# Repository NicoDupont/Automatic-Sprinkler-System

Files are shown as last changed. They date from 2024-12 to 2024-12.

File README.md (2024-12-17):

# Arrosage Automatique

A diy project to automate my irrigation system.  

Last Update : 17/12/2024  
This is the second working version for summer 2024, it will be adapted for 2025 if needeed and time available.

- python scripts improved
- webapp improved
- mqtt improved
- overall improvement of functionality

**Minimum Requirements :**

- A Raspberry pi 2 >= with python 3.8.x

- A webserver for the web app

- A database like mariadb/mysql (not tested with another db)

**Main Goal : replace one or more irrigation controllers and do it by mylself.**    

 **Big Concept :**

- Logic is done by python scripts on a raspberry pi

- Data management is done with an sql data base, mqtt is used to monitor and control the systeme from HA

- UI is based on a web application (home assistant can be used too(with mqtt))

- Sensors data comes from home-assistant/esphome
  
  **Overall functional descriptions :**

- A WebApp allows me to manage each solenoid valve/zone, global parameters, see the latest events, the watering sequence and some data.

- A collection of python scripts are used to open or close the solenoid valves and compute the watering sequence(s). 
  
  - There is a winter/stop, test, sequence on demande, automatic and manual mode
  - The program checks some data to know if it can run watering
  - Status and events are recorded in the database, sent to an mqtt broker and displayed on an LCD screen
  - Several zones and/or sequences can run simultaneously (depends on the power supply for the solenoid valve and the watering pump)

- config.py file is used to configure the script in addition with the database.

- I can bypass the programmation to directly power supply and open any solenoid valve I want with 3 positions switch wired for each solenoid valve.

- Mqtt autodiscovery for homeassistant can be used (first test for diagnostics and not finish actualy)

- There are a few built-in automations : max number of active solenoid valve active at the same time, rainfall, test if one sequence is between 2 days,  calculate the coef duration in correlation with the outside temperature...

**Side projects (in progress) :**

- Tank filling  [link](https://github.com/NicoDupont/esp_remplissage_cuve)
- [in progress] PCB for relays, lcd, rtc module [link](https://github.com/NicoDupont/PCB/tree/main/arrosage)
- Irrigation circuit monitoring  [link](https://github.com/NicoDupont/Monitoring_Arrosage)
- [in progress] Tank monitoring  [link](https://github.com/NicoDupont/Monitoring_Cuve_Arrosage)

**Futur improvements :**

- Mqtt : redo/complete mqtt parts with complete autodiscovery in HA (no need to add entities in configuration.yaml and add cmd/state topic)
- The WebApp will be split into two components: Front + Api Back
- Possibility to put a zone in more than 1 sequence
- Clean and redo the watering box (electricity+electronics)

**Current limitations :**

- A sequence/zone cannot be straddled between 2 days due to the very simple operation of the programming
- All parameters cannot be updated from home assistant
- Events are visible only from the web interface
- web app is not complete

**Folder organisation :**

    | IrriPi
      => | App ( simple web app )
         | Docs  
         | rpi (python logic)
         readme.md

**Raspberry Pi requirements :** 

<b>Config.txt :</b>  
In the event of an unexpected restart, this will allow not to open a solenoid valve by mistake.  
I need to add the following to the config.txt file to force gpio output and high state on gpio during the boot sequence :    

> gpio=4-13=op,dh  
> gpio=16-27=op,dh 

Gpio 2,3 are used for I2C (rtc and lcd)  
Gpio 14-15 are reserved and cannot be used !   

=> 22 gpio are therefore usable  

#### Start Watering at start

<b>Cron :</b>  
in contrab -e:

> @reboot sleep 20; sh /home/pi/launcher_arrosage.sh

<b>best solution by creating services with systemd</b>

For each Python file (main.py, automation.py, mqtt_publish.py mqtt_subscribe.py)

- arrosage-main
- arrosage-automation
- arrosage-publisher
- arrosage-subscriber

```bash
sudo nano /etc/systemd/system/arrosage-main.service

[Unit]
Description=Arrosage Main
After=network-online.target sysinit.target
Wants=network-online.target sysinit.target

[Service]
User=pi
WorkingDirectory=/home/pi/arrosage
ExecStart=/usr/bin/python3 /home/pi/arrosage/main.py
Restart=always
RestartSec=5

[Install]
WantedBy=multi-user.target

#update systemed
sudo systemctl daemon-reload
#enable service
sudo systemctl enable arrosage-main.service
#status
sudo systemctl status arrosage-main.service
#start
sudo systemctl start arrosage-main.service
#stop
sudo systemctl stop arrosage-main.service
#restart
sudo systemctl restart arrosage-main.service
```

<b>Raspi-config :</b>  

- i2c must be activated (rtc + lcd)
- spi must be deactivated  

<b>Mqtt autodiscovery in home assistant :</b>    

> run : python3 /home/pi/arrosage/mqtt_autodiscovery.py     

**Functional Diagram :**

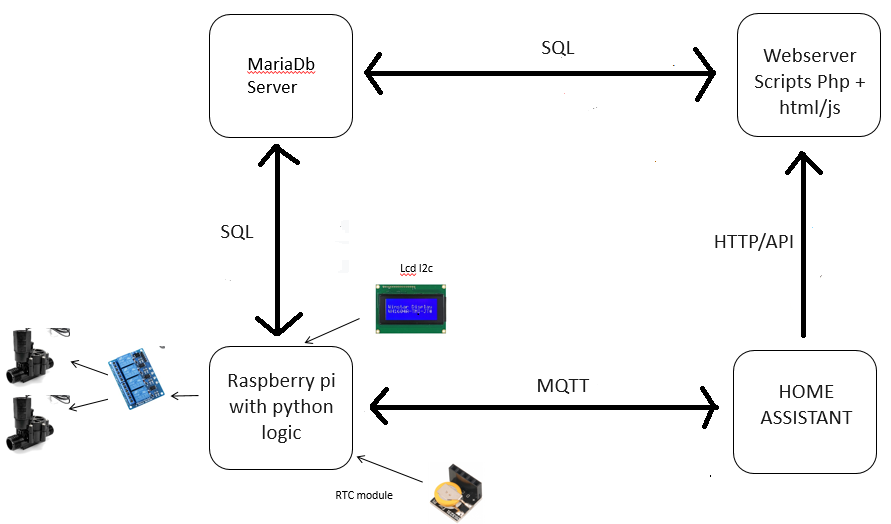
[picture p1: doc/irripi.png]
Functional_Diagram


**Watering parts**

- I use rainbird dv100 24vac solenoid valve

**Electric Parts**

- 1x Circuit breaker 2A 230v
- 1x Electrical outlet 230v
- 1x AC 24v 1,6A output rail din power supply (for solenoid valves) [links](https://www.amazon.fr/gp/product/B00F4QIL06/ref=ppx_yo_dt_b_asin_title_o02_s00?ie=UTF8&psc=1)
- 1x DC 5v 2.5A output power supply (for raspberry, esp8266, relay, electronic...)

Electronics_Box

**Electronics Parts**

- Raspberry Pi 2b + micro sd 
- 22x relay 5v
- 22x button 3 positions
- 1x button 2 positions
- 23x Screw Fuse Terminal Block rail din [links](https://fr.aliexpress.com/item/32957557760.html?spm=a2g0o.order_list.0.0.21ef5e5bLPmCsD&gatewayAdapt=glo2fra)
- 22x fuse 20x5 0.5A
- 1x fuse 20x5 2A
- 1x lcd 20x4 i2c 5v
- 1x rtc module DS3231 i2c 3.3v

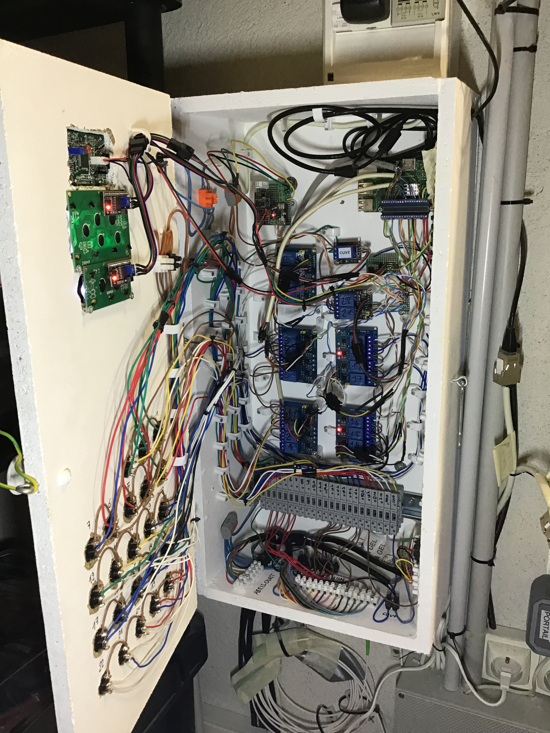
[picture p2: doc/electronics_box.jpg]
Electronics_Box

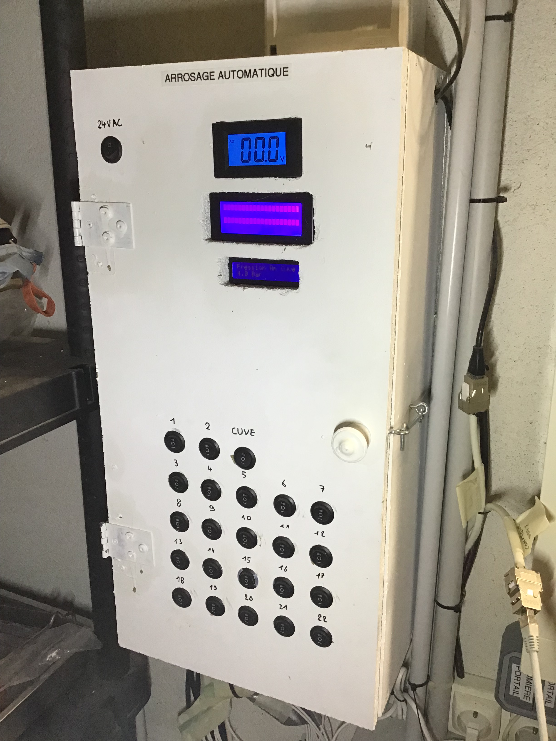
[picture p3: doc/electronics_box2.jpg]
Electronics_Box


**Web App :**

The web app  :  

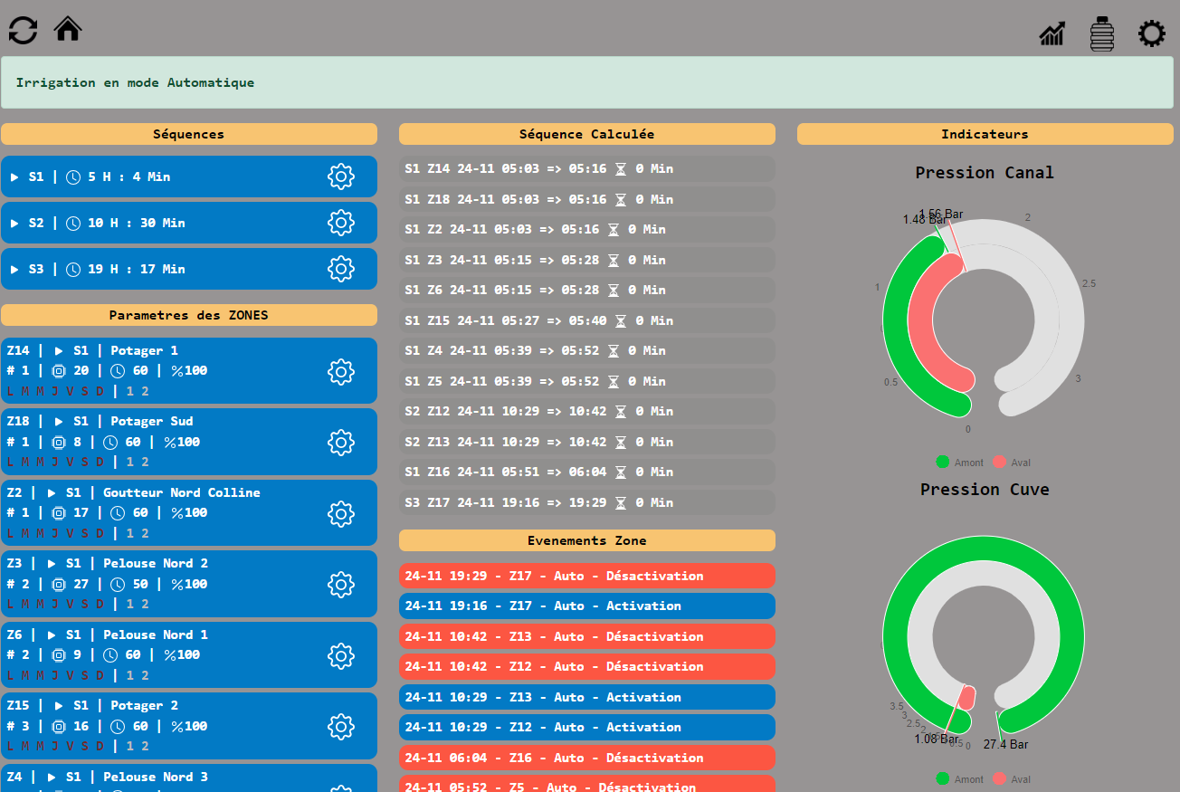
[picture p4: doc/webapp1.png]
web app irripi


**Schematic :**

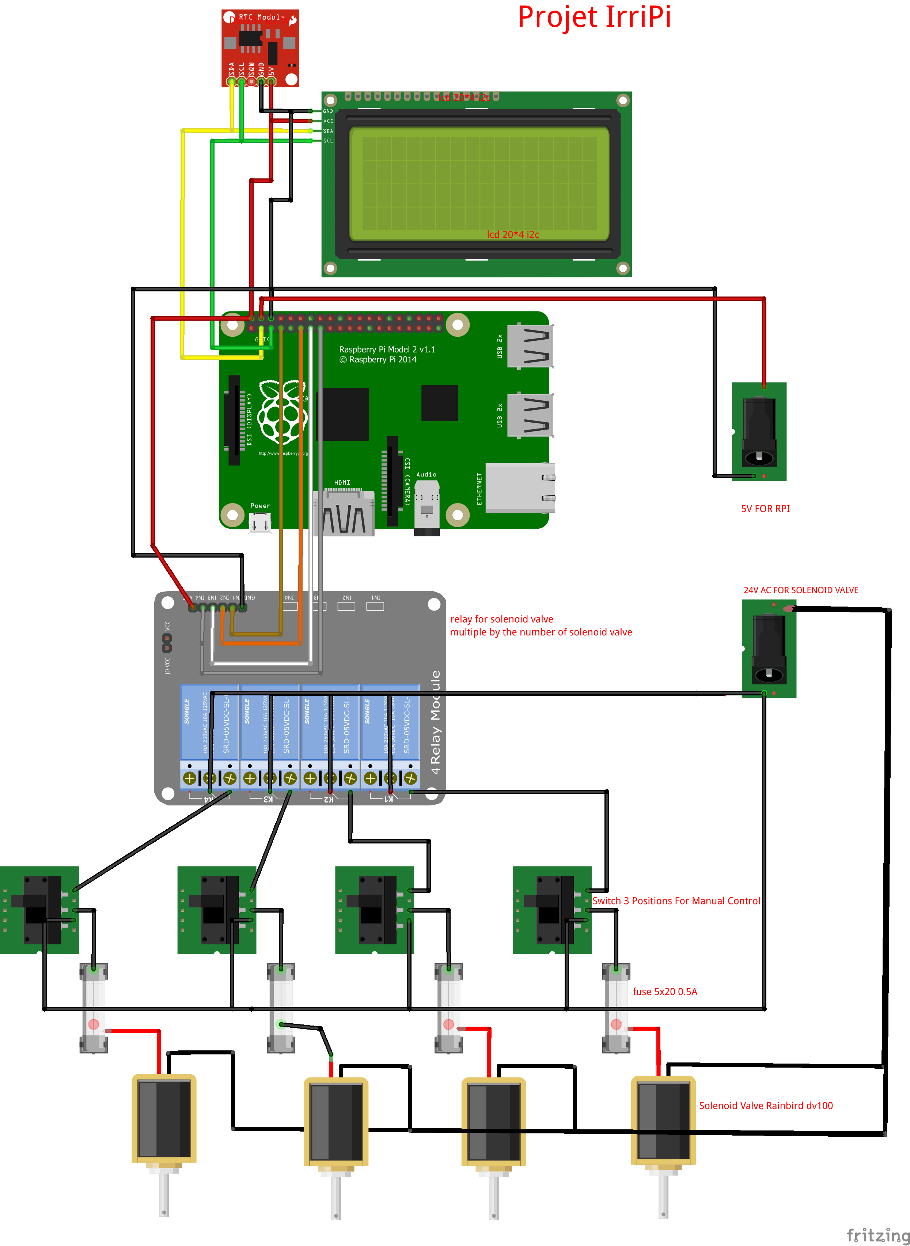
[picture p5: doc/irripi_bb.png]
fritzing irripi rpi


**Integration in [Home-Assistant](https://www.home-assistant.io/)**

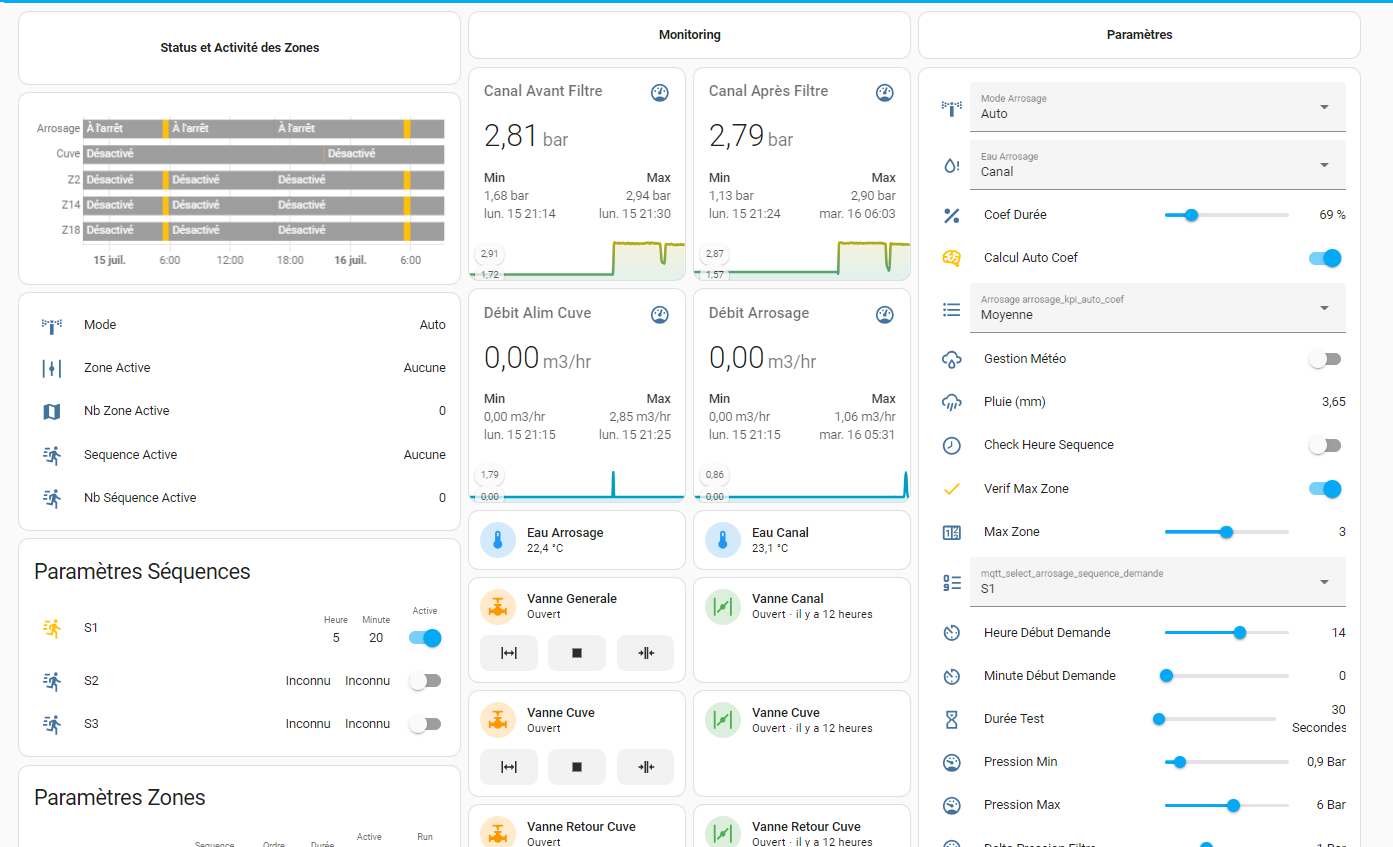
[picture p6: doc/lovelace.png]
Home-Assistant lovelace

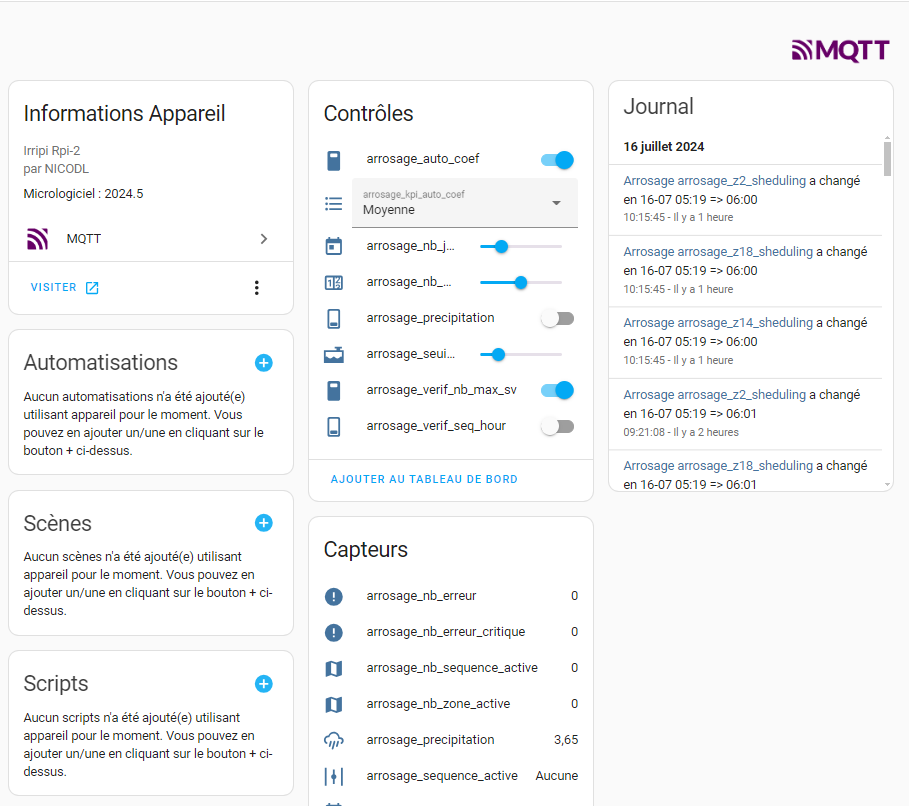
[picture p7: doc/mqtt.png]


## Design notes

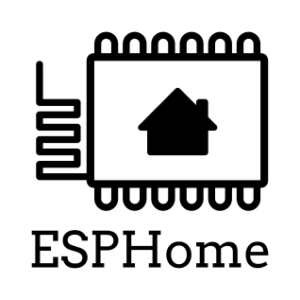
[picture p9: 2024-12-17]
webapp/img/esphome.png

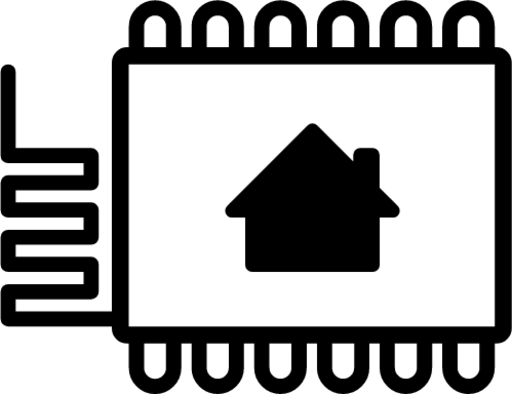
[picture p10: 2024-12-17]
webapp/img/esphome2.png

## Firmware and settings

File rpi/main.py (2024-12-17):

"""
* -----------------------------------------------------------------------------------
* Last update :   24/10/2024
* Arrosage Automatique / IrriPi
* Main launch script
* -----------------------------------------------------------------------------------
"""
#conda install -c conda-forge mysql-connector-python
# if numpy error on raspberrypi :
#sudo apt-get install python-dev libatlas-base-dev 
from watering import Watering
from sequence import ComputeSequence
from anomaly import AnomalyDetection,MqttStatusAnomaly
import function as func
import yaml
import time
import RPi.GPIO as GPIO
#import pandas as pd
import logging
import datetime
import pandas as pd

if __name__ == '__main__':
    #---------------------------------------
    # parameters for the script from config.yaml 
    import config as config

    GPIO.setwarnings(False)
    GPIO.cleanup()
    GPIO.setmode(GPIO.BCM)
    for gpio in config.list_gpio:
        GPIO.setup(gpio, GPIO.OUT)
        GPIO.output(gpio, GPIO.HIGH)

    #--------------------------------------
    #initialise logging config
    #jour = GetDayTime(0)
    logger = logging.getLogger(__name__)#.addHandler(logging.NullHandler())
    #logfile = "log/arrosage_"+str(jour.day)+"_"+str(jour.month)+"_" +str(jour.year)+".txt"
    logfile = "log/arrosage.txt"
    func.ConfigLogging(logger,logfile,config.LOG_LEVEL_STREAM,config.LOG_LEVEL_FILE,True)

    #https://stackoverflow.com/questions/5974273/python-avoid-passing-logger-reference-between-functions
    #---------------------------------------
    # NUMBER_LOOP
    i=0
    cpt_error = 0
    cpt_info = 0
    
    while True: #loop launch
        i+=1
        cpt_info+=1
        try:
            engine,connection = func.DbConnect(logger)
            func.AddMqttQueue(i,"status/loop_main",connection,logger)#to know if running
            func.AddMqttQueue(cpt_error,'status/loop_main_erreur',connection,logger)#to know if error
            try:
                actual_day = func.GetDayTime(0)
                #prev_day = GetDayTime(-1) 
                # ----------------------------------------------------
                # global settings 
                global_settings = func.LoadData('select * from Parameter limit 1',logger,connection,file=config.GLOBAL_SETTINGS_FILE)
                global_coef = global_settings["coef"].iloc[0]
                mode = global_settings["mode"].iloc[0]
                sequence_demande = global_settings["sequence_demande"].iloc[0]
                heure_demande = global_settings["heure_demande"].iloc[0]
                minute_demande = global_settings["minute_demande"].iloc[0]
                logger.debug(f'mode arrosage: {mode}')
                # ----------------------------------------------------
                # sequences settings
                sequence_settings = func.LoadData('select * from Sequence where active=1',logger,connection,file=config.SEQUENCE_FILE)
                # ----------------------------------------------------
                # zones settings
                zone_settings = func.LoadData("""select a.id_sv,a.type,a.sv,a.order,a.gpio,a.name,a.open,
                                              (case when b.active=0 then 0 else a.active end) as active,
                                              a.sequence,a.duration,a.test,a.even,a.odd,a.monday,a.tuesday,
                                              a.wednesday,a.thursday,a.friday,
                                              a.saturday,a.sunday,a.coef,a.rpi 
                                              from Zone as a 
                                              left join Sequence as b on a.sequence=b.seq 
                                              where a.type='zone'""",logger,connection,file=config.ZONE_PARAMETER_FILE)
                logger.debug("Zone:")
                logger.debug(zone_settings.head())
                # ----------------------------------------------------
                # calculate the solenoid valve launch sequence by sequence and order
                zone_active = zone_settings[zone_settings.active.eq(1)]
                logger.debug("Zone active:")
                logger.debug(zone_active.head())
                # ----------------------------------------------------
                # iterate over sequence to compute each sequence 

                ##################################################################################################
                # modifier cette partie car conflit quand plusieurs sequences actives et revoir le mode à la demande
                if not sequence_settings.empty and not zone_active.empty:
                    zone_sequence = pd.DataFrame()
                    for index, row in sequence_settings.iterrows():
                        sequence = row["seq"]
                        hstart = row["heure"]
                        mstart = row["minute"]
                        
                        if mode == 'Demande' and sequence_demande==sequence:
                            starting_date = datetime.datetime(actual_day.year, actual_day.month, actual_day.day,hour=int(heure_demande),minute=int(minute_demande))
                        else:
                            starting_date = datetime.datetime(actual_day.year, actual_day.month, actual_day.day,hour=int(hstart),minute=int(mstart))

                        params_compute_sequence = {
                            'sequence_number':sequence,
                            'reference_date':starting_date,
                            'zone':zone_active[zone_active.sequence.eq(sequence)],
                            'global_time_coefficient':global_coef,
                            'delay_time_sequence':config.DELAY_TIME_SEQUENCE,
                            'min_runtime':config.MIN_TIME_SEQUENCE,
                            'max_runtime':config.MAX_TIME_SEQUENCE,
                            'logger':logger
                        }
                        #calculation of the sequence for the watering zones by sequence number
                        zs = pd.DataFrame()
                        zs = ComputeSequence(**params_compute_sequence)
                        logger.debug("Zone Sequence:")
                        logger.debug(f"zone :{sequence}")
                        logger.debug(zone_sequence.head())
                        if not zs.empty:
                            if zone_sequence.empty:
                                zone_sequence = zs
                            else:
                                zone_sequence = pd.concat([zone_sequence,zs], ignore_index=True)
                            
                    zone_active = zone_active.merge(zone_sequence, how='left', on=['order','sequence'])
                    #filter data if no sequence active and add boolean if sv is planned today.
                    #logger.info(zone_active.head(15))
                    zone_active['planned']=zone_active.apply(lambda row: func.IsProgrammed(row["sv"],row["StartingDate"],row["EndDate"],actual_day,row["even"],row["odd"],row["monday"],row["tuesday"],row["wednesday"],row["thursday"],row["friday"],row["saturday"],row["sunday"],True,logger), axis=1)
                    zone_active= zone_active[zone_active['StartingDate'].notnull()]
                    # update calculated sequences to the database
                    #logger.info(zone_active.head())
                    func.UpdateSequence('SequenceZone',zone_active[['id_sv','sv','name','sequence','order','open','duration','StartingDate','EndDate','planned']],connection,engine,logger)

                else:
                    logger.warning('Aucune sequence ou zone active')
                    #list_columns=['id_sv', 'sv', 'order', 'gpio', 'name', 'open','active', 'sequence', 'duration', 'even', 'odd', 'monday', 'tuesday','wednesday', 'thursday', 'friday', 'saturday', 'sunday', 'coef', 'rpi','StartingDate', 'EndDate']
                    #zone_active = pd.DataFrame(columns=list_columns)
                    #create an empty dataframe if no active zone or sequence
                    zone_active = pd.DataFrame()       #empty dataframe
                    # update calculated sequences to the database
                    func.UpdateSequence('SequenceZone',pd.DataFrame(columns=['id_sv','sv','name','sequence','order','open','duration','StartingDate','EndDate','planned']),connection,logger)

                # dataframe of gpio+sv which are not in the sequence to deactivate them if they were previously active
                zone_inactive = zone_settings[zone_settings.active.ne(1)][["gpio","sv","rpi","open"]]
                if zone_inactive.empty:
                    logger.debug("Aucune zone inactive")
                # ----------------------------------------------------
                # recover pontential anomalies 
                if config.DETECT_ANOMALY:
                    params_anomaly_detection = {
                            'global_settings':global_settings,
                            'IP_WEB_SERVER':config.IP_WEB_SERVER,
                            'IP_HA_SERVER':config.IP_HA_SERVER,
                            'IP_MQTT_SERVER':config.IP_MQTT_SERVER,
                            'IP_WEB':config.IP_WEB,
                            'connection':connection,
                            'logger':logger
                        }
                    anomaly = AnomalyDetection(**params_anomaly_detection)
                    if cpt_info==5:
                        MqttStatusAnomaly(anomaly,connection,logger)
                
                # ----------------------------------------------------
                # opening or closing control of the solenoid valves for watering
                if config.RUN_WATERING: 
                    params_watering = {
                            'iteration':i,
                            'critical_anomaly':anomaly[1],
                            'zone_inactive':zone_inactive,
                            'zone_active':zone_active,
                            'global_settings':global_settings,
                            'rpi_number':config.RPI_NUMBER,
                            'actual_date':actual_day,
                            'connection':connection,
                            'logger':logger
                        }
                    Watering(**params_watering) 
                    if cpt_info==5:
                        cpt_info=0 
                        func.MqttStatusZoneSequence(connection,logger) #push mqtt info about zone and sequence to the brocker
            except Exception as e:
            #else: 
                cpt_error+=1
                logger.exception(f'Erreur main.py msg : {e}')
        #else:
        except Exception as e:
            cpt_error+=1
            logger.exception(f'Erreur connexion bdd main.py msg : {e}')
        finally:
            try:
                func.DbClose(engine,connection,logger)
            except Exception as e:
                cpt_error+=1
                logger.exception(f'Erreur Dbclose Boucle Main msg : {e}')
            # ----------------------------------------------------
            #wait SLEEP_TIME_LOOP seconds for next loop
        time.sleep(config.SLEEP_TIME_LOOP)
        #PublishMqtt(i,"status/loop_main",logger)
        logger.debug("==============     FIN LOOP            ==============")
        logger.debug("=====================================================")
    # ----------------------------------------------------
    #after while => end of the script if we going out off the loop
    GPIO.cleanup()
    logger.error("END LOOP")

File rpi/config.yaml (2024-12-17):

---
p_rpi : 1                                       # rpi number 1 => you can use 1 or more rpi if you don't have enought gpio just run the same program (only main.py) with "2"
p_log_level_stream: "INFO" # log level to be write like print  NOTSET | DEBUG | INFO | WARNING | ERROR | CRITICAL
p_log_level_file: "INFO" # log level to be write in log file   NOTSET | DEBUG | INFO | WARNING | ERROR | CRITICAL
p_name : "IrriPi"                               # project name
p_version : "2024.10"                            # project version
p_date_version : "20/10/2024"                   # date version
p_sleep_loop : 8                                # time in seconds to wait for the next loop
p_watering : true                               # active or not the watering
p_delay_sequence : -15                          # delta time in seconds between two zones (avoid water hammer)  (not use for test and manual mode)                          
p_min_runtime : 1                               # minimum run time in minute for one sequence (not use for test and manual mode)           
p_max_runtime : 180                             # maximum run time in minute for one sequence (not use for test and manual mode)           
p_log_bdd : true                                # log data in the database
p_anomaly : true                                # active the anomalies detection
p_lcd_screen : true                            # active  the lcd
p_lcd_sleep_time : 2                            # sleep time in seconds fort reading the lcd
p_mqtt : true                                  # active the mqtt
p_ip_mqtt : "192.168.1.125"                     # local ip of the mqtt broker
p_ip_ha : "192.168.1.125"                       # local ip of the ha server
p_ip_www : "www.google.com"                       # local ip of the ha server
p_mqtt : true
p_port_mqtt : 1883                              # port number of the mqtt broker
p_user_mqtt : "nicolas"                         # user of the mqtt broker for auth
p_topics_mqtt : "json/topic_mqtt.json"         # lists of mqtt topics to subscibe
P_prefix_mqtt : "ha"                            # name for mqtt automatique discovery in homeassistant
p_device_mqtt : "arrosage"                      # device name for homeassistant
p_sufix_sta_mqtt : "/state"                           # suffix for state topic ?
p_sufix_cmd_mqtt : "/cmd"                           # suffix for command topic ?
p_zp_file : 'json/zone_parameters.json'         # file where the zone settings are stored
p_gp_file : 'json/global_parameters.json'       # file where global settings are stored
p_zone_file : 'json/sequence_zone.json'         # file where the zone sequence is stored
p_sequence_file : 'json/sequence.json'          # file where the sequence is stored
p_az_file : 'json/active_zone.json'             # file where the active valves are stored
p_mqtt_bdd_autodiscovery_file : 'json/mqtt_bdd_autodiscovery.json' # file where mqtt config for mqtt autodiscovery in ha is stored
p_ip_web : "192.168.1.123"                      # local server web ip for web UI
p_database : "ARROSAGE"                         # database name
p_ip_bdd : "192.168.1.123"                       # local ip of the database server
p_user_bdd : "nicolas"                             # user database
p_gpio: [4,17,27,22,10,9,11,5,6,13,19,26,21,20,16,12,7,8,25,24,23,18]  # list of gpio for this rpi
p_min_coef : 20
p_max_coef : 200
p_min_coef_temp : 20
p_max_coef_temp : 45

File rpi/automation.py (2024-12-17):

"""
* -----------------------------------------------------------------------------------
* Last update :   15/12/2024
* Arrosage Automatique / IrriPi
* Script for automations, diagnostics data and lcd management
* -----------------------------------------------------------------------------------
"""

#import function as func
from function import DbClose,UpdateJson,SynchroMqtt,UpdateSequenceTime,DbPurge,UpdateZoneOrder,CheckTotalPrecipitation,UpdateCoef,GetOsName,GetDiskUsage,GetLocalIp,GetPythonVersion,GetLoadAverage,ConfigLogging,Print2Lcd,DbConnect,AddMqttQueue,LoadData,GetDayTime,GetCpuTemperature,GetUptime,GetMemoryUsage,MqttStatusZoneSequence,MqttProgZone,DisplaySequence,DisplayActiveZone
from anomaly import AnomalyDetection
import lcddriver  #comment if not lcd
import yaml
import logging
import time
# parameters 
import config as config


if __name__ == '__main__':
    #--------------------------------------
    #initialise logging config
    #actual_day = GetDayTimeNtp(0,logger)
    logger = logging.getLogger(__name__)#.addHandler(logging.NullHandler())
    #logfile = "log/automation_"+str(actual_day.day)+"_"+str(actual_day.month)+"_" +str(actual_day.year)+".txt"
    logfile = "log/automation.txt"
    ConfigLogging(logger,logfile,config.LOG_LEVEL_STREAM,config.LOG_LEVEL_FILE,True)


    if config.ACTIVE_LCD:
        #initialise the lcd screen
        try:
            lcd = lcddriver.lcd()
            Print2Lcd(lcd,config.WAIT_TIME_LCD,True,"{0} {1} {2}".format(config.PROJECT_NAME,config.PROJECT_VERSION,config.PROJECT_DATE_VERSION),"Demarrage !","","",logger) 
            Print2Lcd(lcd,config.WAIT_TIME_LCD,False,"","Initialisation..."," "," ",logger) 
        except Exception as e:
            logger.exception(f"Probleme initialisation du lcd msg : {e}")
        

    cpt=0
    cpt_automation=0
    cpt_diagnostic=0
    cpt_error=0

    while True:

        cpt+=1
        cpt_automation+=1
        cpt_diagnostic+=1
        
        engine1,connection1 = DbConnect(logger)
        
        AddMqttQueue(cpt,'status/loop_automation',connection1,logger)#to know if running
        AddMqttQueue(cpt_error,'status/loop_automation_erreur',connection1,logger)#to know if error
        
        global_settings = LoadData('select * from Parameter limit 1',logger,connection1,file=config.GLOBAL_SETTINGS_FILE)
        MODE = global_settings["mode"].iloc[0]
        AUTO_COEF = global_settings["auto_coef"].iloc[0]
        KPI_AUTO_COEF = global_settings["kpi_auto_coef"].iloc[0]
        SEQUENCE_HOUR = global_settings["verif_seq_hour"].iloc[0]
        PRECIPITATION = global_settings["precipitation"].iloc[0]
        RAIN_THRESHOLD = global_settings["seuil_precipitation"].iloc[0]
        JOUR_PRECIPITATION = global_settings["nb_jour_precipitation"].iloc[0]
        CUMUL_PRECIPITATION = global_settings["cumul_precipitation"].iloc[0]
        STR_PRECIPITATION = "OUI" if global_settings["precipitation"].iloc[0] == 1 else "NON"
        actual_day = GetDayTime(0)
        str_kpi_auto_coef = KPI_AUTO_COEF if AUTO_COEF==1 else "none"
        str_auto_coef = "OUI" if AUTO_COEF==1 else "NON"
        
        
        try:
            if config.ACTIVE_LCD:
                Print2Lcd(lcd,config.WAIT_TIME_LCD,True,"","Mise a jour :","Parametres"," ",logger) 
                params_anomaly_detection = {
                        'global_settings':global_settings,
                        'IP_WEB_SERVER':config.IP_WEB_SERVER,
                        'IP_HA_SERVER':config.IP_HA_SERVER,
                        'IP_MQTT_SERVER':config.IP_MQTT_SERVER,
                        'IP_WEB':config.IP_WEB,
                        'connection':connection1,
                        'logger':logger
                    }
                anomaly = AnomalyDetection(**params_anomaly_detection)
                critique = "OUI" if anomaly[0] and anomaly[1] else "NON"
                Print2Lcd(lcd,config.WAIT_TIME_LCD,True,"Date : ","{0}-{1}-{2} {3}:{4}".format('0'+str(actual_day.day) if actual_day.day<10 else actual_day.day,'0'+str(actual_day.month) if actual_day.month<10 else actual_day.month,actual_day.year,'0'+str(actual_day.hour) if  actual_day.hour<10 else actual_day.hour,'0'+str(actual_day.minute) if  actual_day.minute<10 else actual_day.minute),"","",logger)
                if anomaly[0]:
                    Print2Lcd(lcd,config.WAIT_TIME_LCD,True,f"Nb Erreur : {str(len(anomaly[2]))}","Erreur Critique : ",critique,"",logger)
                    Print2Lcd(lcd,config.WAIT_TIME_LCD,True,"Liste Anomalie :","","","",logger)
                    for error, msg in anomaly[2].items():
                        Print2Lcd(lcd,config.WAIT_TIME_LCD,True,f"Erreur numero : {str(error)}","Message =>",msg,"",logger)
                Print2Lcd(lcd,config.WAIT_TIME_LCD,True,"Calcul Auto Coef :",str_auto_coef,"Methode :",str_kpi_auto_coef,logger)
                Print2Lcd(lcd,config.WAIT_TIME_LCD,True,"Arrosage",f"Mode : {MODE}","","",logger) 
                Print2Lcd(lcd,config.WAIT_TIME_LCD,True,f"Test Pluie : {STR_PRECIPITATION}",f'Nb Jour : {JOUR_PRECIPITATION}',f'{CUMUL_PRECIPITATION} mm / {RAIN_THRESHOLD} mm',f"Mode : {global_settings['mode'].iloc[0]}",logger)
                DisplaySequence(lcd,config.WAIT_TIME_LCD,connection1,logger)
                DisplayActiveZone(lcd,config.WAIT_TIME_LCD,connection1,logger)
                
                AddMqttQueue(cpt,'status/loop_lcd',connection1,logger)
                
        except Exception as e:
            cpt_error+=1
            logger.exception(f'Erreur automation.py partie LCD msg : {e}')
        
        try:   
            if cpt_diagnostic==3:
                cpt_diagnostic=0
                AddMqttQueue(GetCpuTemperature(logger),"status/temperature_cpu",connection1,logger)
                AddMqttQueue(GetUptime(logger),"status/uptime",connection1,logger)
                AddMqttQueue(GetMemoryUsage(logger),"status/memory_usage",connection1,logger)
                AddMqttQueue("online","status/available",connection1,logger) #for availability if use
                MqttProgZone(connection1,logger)
                AddMqttQueue(MODE,'status/mode',connection1,logger)
                AddMqttQueue(cpt,'status/loop_diagnostic',connection1,logger)#to know if error
                
        except Exception as e:
            cpt_error+=1
            logger.exception(f'Erreur automation.py partie diagnostic msg : {e}')
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
